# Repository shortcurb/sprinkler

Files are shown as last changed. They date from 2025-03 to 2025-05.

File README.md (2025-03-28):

# sprinkler
For controlling my house sprinklers with a Raspberry Pi and a custom PCB

mqttclient.service handles the MQTT listening for commands and sending responses
sprinklerer.service handles the GPIO pin changing to control different relays
scheduler.service handles checking for weather and sunrise/sunset (solar) data

sprinklerer interacts with other modules purely through redis/celery
I needed an abstraction layer that has exclusive control over the GPIOs to prevent all manner of negative effects with the sprinklers including:
* More than one zone turning on at a time
* Turning more than one zone off at a time (water hammer possible)
* Thinking I turned all the relays/zones off, but then some dormant zombie process coming back and turning one/more back on
* Some other process crashing and leaving the zones turned on forever

scheduler handles 

mqttclient is the only other module that interacts via redis/celery, just adding and cancelling sprinkling and stopping tasks

scheduler handles 

To Do:
* Pull any sensitive info out and put it in a .env and .gitignore it
* Rethink the queuing system. I have no visibility into the Celery thing
    * Maybe there's a way I can handle a queue within python? Have the scheduler spin up a process and do it? Something with async?

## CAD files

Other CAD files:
sprinkler_Fusion360/Sprinkler Case v5.f3d

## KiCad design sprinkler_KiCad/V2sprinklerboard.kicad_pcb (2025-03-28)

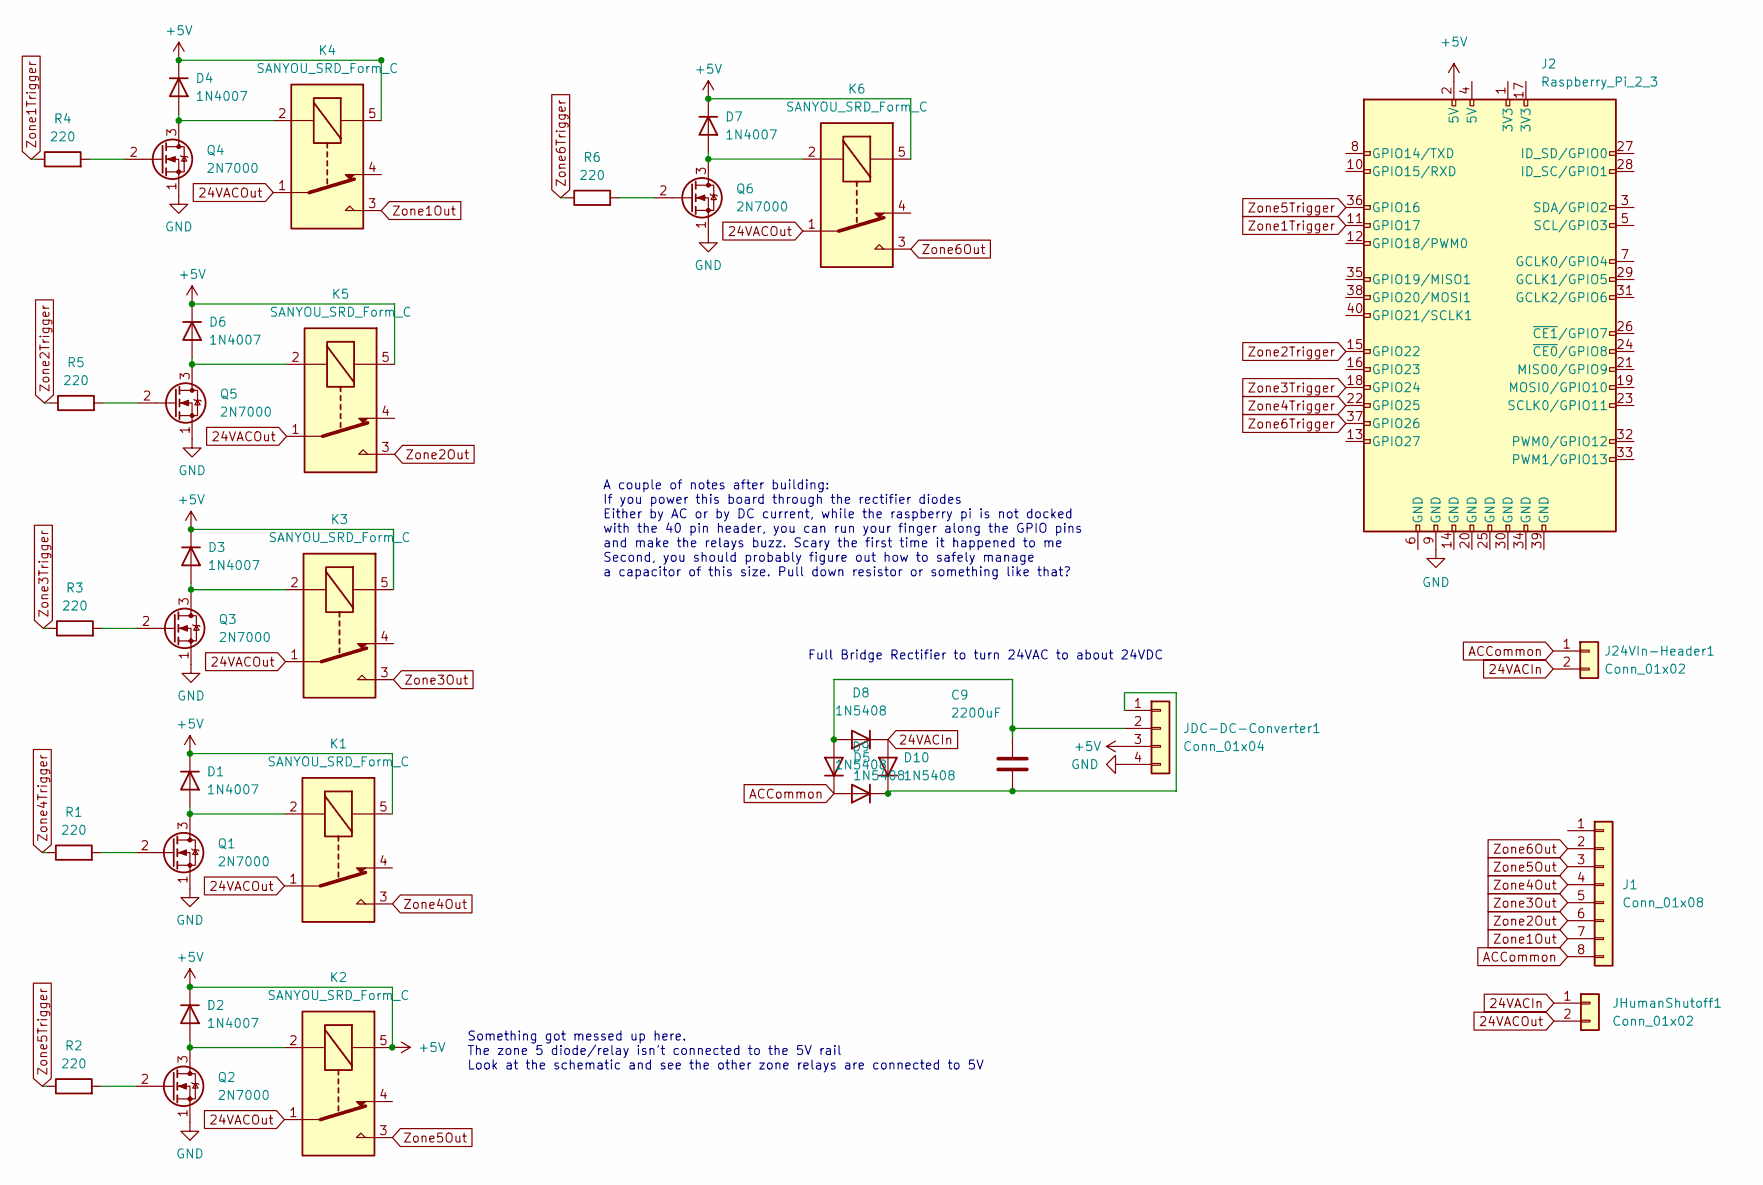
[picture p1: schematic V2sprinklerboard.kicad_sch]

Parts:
C9: 2200uF; C_Radial_D16.0mm_H25.0mm_P7.50mm
D1, D2, D3, D4, D6, D7: 1N4007; D_DO-41_SOD81_P10.16mm_Horizontal
D5, D8, D9, D10: 1N5408; D_DO-201AD_P15.24mm_Horizontal
J1: Conn_01x08; TerminalBlock_Phoenix_MKDS-1,5-8_1x08_P5.00mm_Horizontal
J2: Raspberry_Pi_2_3; RPi Full size -AE
J24VIn-Header1: Conn_01x02; TerminalBlock_Phoenix_MKDS-1,5-2_1x02_P5.00mm_Horizontal
JDC-DC-Converter1: Conn_01x04; XL6009E1 DC-DC
JHumanShutoff1: Conn_01x02; JST_EH_B2B-EH-A_1x02_P2.50mm_Vertical
K1, K2, K3, K4, K5, K6: SANYOU_SRD_Form_C; Relay_SPDT_SANYOU_SRD_Series_Form_C
Q1, Q2, Q3, Q4, Q5, Q6: 2N7000; TO-92_Inline
R1, R2, R3, R4, R5, R6: 220; R_Axial_DIN0411_L9.9mm_D3.6mm_P12.70mm_Horizontal

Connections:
24VACIn: D8.1 (K), D10.2 (A), J24VIn-Header1.2, JHumanShutoff1.1
24VACOut: JHumanShutoff1.2, K1.1, K2.1, K3.1, K4.1, K5.1, K6.1
+5V: D1.1 (K), D3.1 (K), D4.1 (K), D6.1 (K), D7.1 (K), J2.2 (5V), JDC-DC-Converter1.3, K1.5, K3.5, K4.5, K5.5, K6.5
ACCommon: D5.1 (K), D9.2 (A), J1.8 (INT), J24VIn-Header1.1
GND: J2.9 (GND), JDC-DC-Converter1.4, Q1.1 (S), Q2.1 (S), Q3.1 (S), Q4.1 (S), Q5.1 (S), Q6.1 (S)
unnamed: C9.1, D5.2 (A), D8.2 (A), JDC-DC-Converter1.2
unnamed: C9.2, D9.1 (K), D10.1 (K), JDC-DC-Converter1.1
unnamed: D1.2 (A), K1.2, Q1.3 (D)
unnamed: D2.1 (K), K2.5
unnamed: D2.2 (A), K2.2, Q2.3 (D)
unnamed: D3.2 (A), K3.2, Q3.3 (D)
unnamed: D4.2 (A), K4.2, Q4.3 (D)
unnamed: D6.2 (A), K5.2, Q5.3 (D)
unnamed: D7.2 (A), K6.2, Q6.3 (D)
unnamed: Q1.2 (G), R1.2
unnamed: Q2.2 (G), R2.2
unnamed: Q3.2 (G), R3.2
unnamed: Q4.2 (G), R4.2
unnamed: Q5.2 (G), R5.2
unnamed: Q6.2 (G), R6.2
Zone1Out: J1.7 (AD0), K4.3
Zone1Trigger: J2.11 (GPIO17), R4.1
Zone2Out: J1.6 (XDA), K5.3
Zone2Trigger: J2.15 (GPIO22), R5.1
Zone3Out: J1.5 (XCL), K3.3
Zone3Trigger: J2.18 (GPIO24), R3.1
Zone4Out: J1.4 (SDA), K1.3
Zone4Trigger: J2.22 (GPIO25), R1.1
Zone5Out: J1.3 (SCL), K2.3
Zone5Trigger: J2.36 (GPIO16), R2.1
Zone6Out: J1.2 (Pin2), K6.3
Zone6Trigger: J2.37 (GPIO26), R6.1

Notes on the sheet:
A couple of notes after building: If you power this board through the rectifier diodes Either by AC or by DC current, while the raspberry pi is not docked with the 40 pin header, you can run your finger along the GPIO pins and make the relays buzz. Scary the first time it happened to me Second, you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
Something got messed up here. The zone 5 diode/relay isn't connected to the 5V rail Look at the schematic and see the other zone relays are connected to 5V
Full Bridge Rectifier to turn 24VAC to about 24VDC

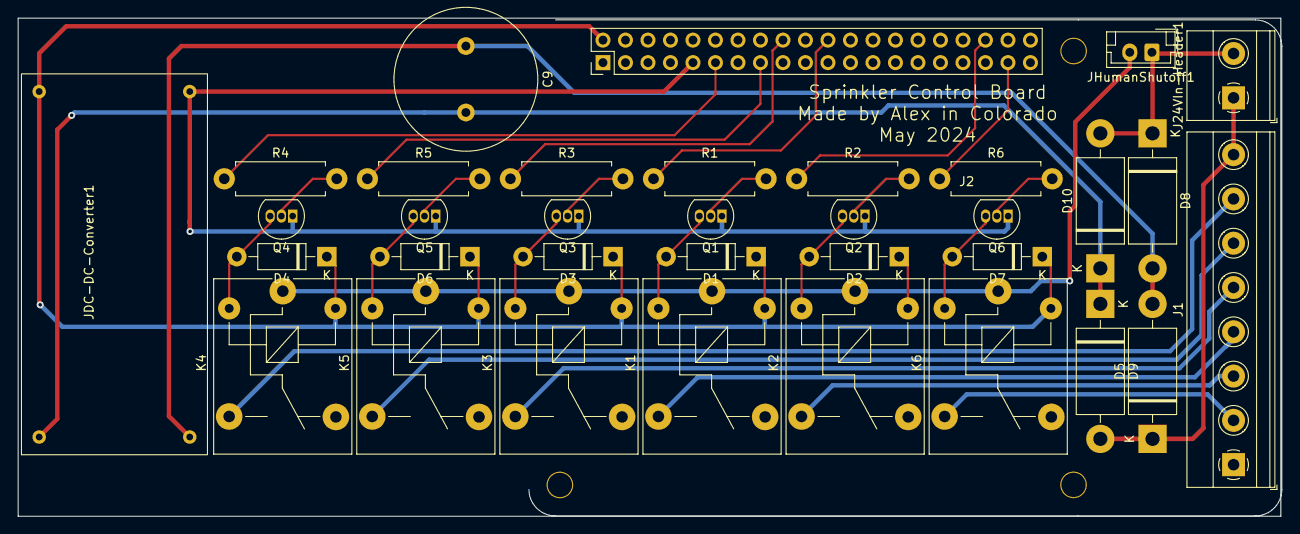
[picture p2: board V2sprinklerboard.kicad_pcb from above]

Board: 2 copper layers, 142.5 x 56.2 mm, 34 parts (0 on the bottom side), 32 nets.

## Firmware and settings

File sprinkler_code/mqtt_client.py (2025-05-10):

import datetime,json,os,traceback,time,asyncio
import paho.mqtt.client as mqtt
from dotenv import load_dotenv
from redis_crud import ScheduleJob, ActiveJob, DataCrud
from gather_data import DataGather


class SprinkleClient:
    def __init__(self):
        load_dotenv()
        self.connected = False
        self.broker_ip = os.environ['mqttbroker']
        self.broker_port = int(os.environ['mqttport'])
        self.username = os.environ['mqttusername']
        self.password = os.environ['mqttpassword']

        self.statetopic = os.environ['mqttsprinklerstatetopic']
        self.cmdtopic = os.environ['mqttsprinklercmdtopic']
        self.responsetopic = os.environ['mqttsprinklerresposnetopic']

        self.commands = ['rain_delay','delay_stop','manual_sprinkle','remove_delay','gather_and_compute', 'skip_next','unskip_next']

    def connect_mqtt(self):
        # Handle reconnection logic elsewhere, just purely connecting here
        if self.connected:
            print('Already connected')
        else:
            self.mqtt_client = mqtt.Client()
            self.mqtt_client.on_message = self.on_message
            self.mqtt_client.on_disconnect=self.on_disconnect
            self.mqtt_client.on_connect = self.on_connect
            self.mqtt_client.username_pw_set(self.username, self.password)
            self.mqtt_client.connect(self.broker_ip, self.broker_port, 60)
            self.connected = True

    def publish_message(self,topic,message):
        if not hasattr(self,'mqtt_client'):
            self.connect_mqtt()

        if isinstance(message,dict):
            message = json.dumps(message,default=str,indent=2)
        try:
            result = self.mqtt_client.publish(topic, message)
        except Exception as e:
            traceback.print_exc()
            self.connected = False
            self.on_disconnect()
            # Let other parts handle the reconnection logic
    
    def gather_and_compute(self,payload):
        print('gathering and computing')
        now = int(time.time())
        sj = ScheduleJob()
        jobs = sj.get_all_jobs()
        job_imminent = False
        for job_id, job_info in jobs.items():
            if job_info['is_cancelled'] !=True and now>job_info['start_at'] and now < job_info['end_at']:
                job_imminent = True
        if job_imminent == False:
            dg = DataGather()
            asyncio.run(self._async_gather_and_compute(dg))

    async def _async_gather_and_compute(self, dg):
        weather_task = asyncio.create_task(dg.get_weather())
        solar_task = asyncio.create_task(dg.get_solar())
        await asyncio.gather(weather_task, solar_task)
        await dg.compute_next_run()

    def delay_stop(self,payload):
        #    payload looks like this: msg = {'command':'delay_stop','value':5,'units':'minutes'}
        # or payload looks like this: msg = {'command':'delay_stop','value':2,'units':'hours'}
        # A delay_stop <=10m is a delay, to be resumed
        # a delay_stop >10m is a stop, with cancellations
        sj = ScheduleJob()
        dc = DataCrud()
        now = int(time.time())
        delay_seconds = datetime.timedelta(**{payload['units']:payload['value']}).total_seconds()
        delay_until = int(now + delay_seconds)
        delay_until_dt = datetime.datetime.now() + datetime.timedelta(seconds = delay_seconds)
        delay_info = {'delay_stop_received_at':now,'delay_stop_until_s':delay_until,'delay_stop_until_dt':delay_until_dt}
        dc.update_data('delaystopinfo',delay_info)
        msg = "Delay/stop request received"
        for job_id,job_info in sj.get_all_jobs().items():
            # if the job isn't cancelled and ( the it starts before the delay or ends before the delay and it hasn't already completed)
            if (job_info['start_at'] < delay_until or job_info['end_at'] < delay_until) and job_info['is_cancelled'] != True and now<job_info['end_at']:
                if delay_seconds <=600:
                    sj.reschedule_existing_job(now,job_id, delay_seconds)
                    msg = f"Delaying until {delay_until_dt}, will resume then"
                else:
                    print('cancelling job',job_id)
                    sj.cancel_job(job_id,now)
                    msg = f"Cancelling jobs through {delay_until_dt}"
                print(msg)
        message = {'received_cmd':'stop','response':msg}
        self.publish_message(self.responsetopic,message)

    def skip_next(self,payload):
        sj = ScheduleJob()
        now = int(time.time())
        next_job_id = None
        next_job_info = {'start_at':now+10**10} 
        
        for job_id,job_info in sj.get_all_jobs().items():
            if job_info['is_cancelled'] == False and job_info['is_active'] == False and job_info['start_at'] > now and now < next_job_info['start_at']:
                next_job_id = job_id
                next_job_info = job_info
                
        print(next_job_id)
#        print('next_job_info',json.dumps(next_job_info,indent=2))
        sj.cancel_job(next_job_id,now)
        message = {'received_cmd':'skip_next','response':f"Skipping next job {next_job_id}"}
        self.publish_message(self.responsetopic,message)

    def unskip_next(self,payload):
        sj = ScheduleJob()
        now = int(time.time())
        next_job_id = None
        next_job_info = {'start_at':now+10**10} 
        for job_id,job_info in sj.get_all_jobs().items():
            if job_info['is_cancelled'] == True and job_info['start_at'] > now and now < next_job_info['start_at']:
                next_job_id = job_id
                next_job_info = job_info
        print(next_job_id)
        sj.uncancel_job(next_job_id)


    def remove_delay(self,payload):
        dc = DataCrud()
        dc.update_data('delaystopinfo',{})

    def manual_sprinkle(self,payload):
    #    payload looks like this: msg = {'command':'manual_sprinkle','value':[[1,5],[2,7],[3,4]],'units':None}
        sj = ScheduleJob()
        now = int(time.time())
        job_info = {
            'start_at':now,
            'zone_info':payload['value'],
            'source':'manual'
                    }
        try:
            job_id = sj.create_job(job_info)
            message = f"Manually created job with id {job_id}"
        except ValueError as e:
            message = e
        self.publish_message(self.responsetopic,{'received_cmd':'manual_sprinkle','response':message})

    def subcribe_loop(self):
#        self.on_disconnect('','','')
        self.connect_mqtt()
        self.mqtt_client.subscribe(self.cmdtopic)
        self.mqtt_client.loop_forever()

    def on_connect(self,client, userdata, flags, rc):
        if rc == 0:
            self.publish_message(self.statetopic,'Posting states here')
            self.publish_message(self.responsetopic,'Starting MQTT client listener')
            self.publish_message(self.cmdtopic,'Listening for commands here')
            print("Connected to broker")
        else:
            print("Connection failed with code", rc)

    def on_disconnect(self,client=None,userdata=None,rc=None):
        self.connected = False
        print('Unexpected disconnection from MQTT broker')
        while self.connected == False:
            try:
                self.connect_mqtt() # connect_mqtt handles setting self.connected to True
                # self.connect_mqtt will also raise an exception if if fails, so put the sleep in the except
                self.subscribe_loop()
            except KeyboardInterrupt:
                return
            except: 
                print('Waiting 5 seconds then attempting reconnection')
#                traceback.print_exc()
                time.sleep(5)

    def on_message(self,client, userdata, msg):
        try:
            payload = msg.payload.decode()
            print(f"Received message: {payload} on topic: {msg.topic}")
            if msg.topic == self.cmdtopic:
                payload = json.loads(payload)
                if payload['command'] in self.commands:
                    getattr(self,payload['command'])(payload) # This calls the given function and executes it with the payload as an argument
        except json.decoder.JSONDecodeError:
            # Only pay attention to json-encoded data
            pass
        except KeyboardInterrupt:
            return
        except Exception as e:
            traceback.print_exc()


if '__main__' == __name__:
    mc = SprinkleClient()
    mc.subcribe_loop()



"""
This thing will have to consist of three separate entities that work together, probably through redis. 
So the structure of data in redis is very important
The sprinkler should handle everything related to atruclly controlling the sprinklers
It will receive a data structure that has a datetime, a list of zones, 
If it has the datetime, is it then the scheduler that decides when to sprinkle?
I guess, yeah. while True: check queue time.sleep(3)
Also I like the idea of keeping datetimes in unix epocs. Makes for easier math
Okay so the sprinkler has a while True loop that checks the queue
The data structure in the queue should be a list of jobs
Jobs should have a datetime start, "active" boolean "cancelled" boolean,
maybe "source" for scheduled vs manual
also datetimes for scheduled at, cancelled at, ran at, etc
Each job needs a unique hash as well

There will also be a redis structure about the current job
When the current job is being executed, it should load that job
into this structure, and update it regularly with current zone,  
time sprinkled, time remaining, next zone, previous zone, expected end datetime
Maybe a cancelled boolean here as well? No.
The cancellation boolean live in the job and the tri-second sprinklerer check the job structure
for cancellation info every 3s?

Then also set up the weather and solar info getting to run via crontab and update redis
And a different (or maybe the same module, different functions?) function
will add jobs to the queue based on solar and weather data
Maybe this system will also clear old jobs out of the queue that are older than e.x. a week?


How do I queue upcoming jobs and make sure they don't overlap?
Maybe I need an intermediary CRUD system that will sit between the job queue
And the systems that might want to CRUD on it?
Yeah I ike that plan
"""




"""

    def delay(self,payload):
    #    payload looks like this: msg = {'command':'delay','value':5,'units':'minutes'}
        now = time.time()
        delay_seconds = datetime.timedelta(**{payload['units']:payload['value']}).total_seconds()
        delay_until = int(now + delay_seconds)
        delay_until_dt = datetime.datetime.now() + datetime.timedelta(**{payload['units']:payload['value']})
        sj = ScheduleJob()
        # don't worry about managing the jobs here
        for job_id,job_info in sj.get_all_jobs():
            if (job_info['start_at'] < delay_until or job_info['end_at'] < delay_until) and job_info['is_cancelled'] != True:
                if job_info['is_active'] == True:
                    print('this is where the computation comes in')
                else:
                    self.sj.reschedule_existing_job(now,job_id,delay_seconds)
            else:
                # really pass, the delay doesn't affect it
                pass
        

    again, what's the interaction between delay and stop?
    A delay implies a resumption,stop implies no resumption
    Maybe have one receipt payload that splits?
    If the payload indicates a timeframe greater than 10 minutes, consider it a stop?
    I think that's it. A delay is, for example to get off the deck when the sprinklers start
    A stop is, e.g. a rain stop or you need to do maintainence on the sprinkler system


 
    def stop(self,payload):
    #    payload looks like this: msg = {'command':'stop':'value':1,'units':'hours}
        now = time.time()
        delay_seconds = datetime.timedelta(**{payload['units']:payload['value']}).total_seconds()
        delay_until = int(now + delay_seconds)
        delay_until_dt = datetime.datetime.now() + datetime.timedelta(**{payload['units']:payload['value']})
        sj = ScheduleJob()
        all_jobs = sj.get_all_jobs()
        for job_id,job_info in all_jobs.items():
            if job_info['start_at'] < delay_until:
                job_info.update({
                    'is_cancelled':True,
                    'cancelled_at':now
                })
                sj.update_job(job_id,job_info)

        # Cancel by creating an immediate job for zone 7 to have a duation of the requested delay_seconds
        # add in stuff about skip for a time to the redis structure that holds that

        msg = {'received_cmd':'stop','response':f"stopping, manual delay until {delay_until_dt}"}
        self.publish_message(self.responsetopic,msg)


"""

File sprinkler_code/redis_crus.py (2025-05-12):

import redis, secrets, string, json,time,traceback
from typing import Dict, Any, List, Optional, Union


class ScheduleJob:
    def __init__(self):
        self.redisclient = redis.Redis(host='localhost', port=6379)

    def uncompute_existing_job(self,job_info): # this is silly
        rudimentary_zones = []
        for item in job_info['zone_info']:
            rudimentary_zones.append([
                item['zone'],(item['end_at']-item['start_at']).total_seconds()/60
            ])
        job_info.update({
            'zone_info':rudimentary_zones,
        })
        return(job_info)

    def reschedule_existing_job(self, now, job_id, delay_s):
        job_info = self.get_job(job_id)
        self.cancel_job(job_id)
        for item in job_info['zone_info']:
            # if the zone hasn't yet been sprinkled, start and end are delayed equally
            # elif the zone is in the middle of being sprinkled, move the start to now + delay and keep the end as end + delay
            # (else) if the zone has already been sprinkled, forget about it
            print(json.dumps(item,indent=2))
            if now < item['on_at'] and now < item['off_at']:
                on_time = item['on_at'] + delay_s
            elif now > item['on_at'] and now < item['off_at']:
                on_time = now + delay_s - 5 # to account for the overlap
            item.update({
                    'on_at':int(on_time),
                    'off_at':int(item['off_at']+delay_s)
                })    
        job_info.update({
            'start_at': int(job_info['zone_info'][0]['on_at']),
            'end_at':int(job_info['end_at'] + delay_s)
        })
        try:
            self.check_for_existing(job_info)
            self.update_job(job_id,job_info)
        except ValueError:
            return('Delayed job interfers with another scheduled job, deleting this one and defering to following. ')

    def compute_new_job(self,job_info):
        start_at = job_info['start_at']
        new_job_info = {
            'start_at':start_at,
            'zone_info':[],
            'source':job_info['source']
        }
        counted_seconds = 0
        for item in job_info['zone_info']:
            duration = item[1] * 60
            zone_info_active = {
                'zone':item[0],
                'on_at':int(start_at + counted_seconds),
                'off_at':int(start_at + counted_seconds + duration + 5)
            }
            new_job_info['zone_info'].append(zone_info_active)
            counted_seconds += duration
        new_job_info.update({
            'end_at':int(start_at + counted_seconds - 5)
        })
        return new_job_info

    def check_for_existing(self,job_id, job_info: Dict):
        job_start = job_info['start_at']
        job_end = job_info['end_at']
        existing_jobs = self.get_all_jobs()

        for existing_job_id,existing_job_info in existing_jobs.items():
            if existing_job_info['is_cancelled'] != True and existing_job_id !=job_id: # only worry about clashes with different jobs and non-cancelled jobs
                if job_start >= existing_job_info['start_at'] and job_start <= existing_job_info['end_at']:
                    raise ValueError(f"Job {job_id} scheduled to start during existing job {existing_job_id}")
                elif (job_end >= existing_job_info['start_at'] and job_end <= existing_job_info['end_at']):
                    raise ValueError(f"Job scheduled to end during existing job {existing_job_id}")

    def get_all_jobs(self):
        jobs = {}
        for key in self.redisclient.scan_iter("jobs:*"):
            job_data = self.redisclient.get(key)
            if job_data:
                jobs.update({key.decode('utf-8'):json.loads(job_data)})
        return jobs       

    def create_job(self,job_info: Dict):
        job_info = self.compute_new_job(job_info)
        try:
            job_id = ''.join(secrets.choice(string.ascii_letters + string.digits) for _ in range(8))
            self.check_for_existing(job_id,job_info)
            job_info.update({
                'created_at':int(time.time()),
                'updated_at':None,
                'cancelled_at':None,
                'is_cancelled':False,
                'is_active':False,
                })
#            print(json.dumps(job_info,indent=2))
            self.redisclient.set(f"jobs:{job_id}",json.dumps(job_info), ex = 60 * 60 * 24 *7)
            return job_id
        except ValueError as e:
            traceback.print_exc()
            print(e)
            return e

    def get_job(self, job_id: str):
        if 'jobs:' not in job_id:
            job_id = f"jobs:{job_id}"
        job_data = self.redisclient.get(job_id)
        if job_data:
            return json.loads(job_data)
        return None

    def update_job(self,job_id: str, update_job: Dict):
        try:
            if update_job['is_cancelled'] != True: # only check for existing if the one you're updating isn't a cancellation
                self.check_for_existing(job_id,update_job)
            update_job.update({'updated_at':int(time.time())})
            self.redisclient.set(job_id,json.dumps(update_job), ex = 60 * 60 * 24 *7)
        except ValueError as e:
            print('i am here')
            traceback.print_exc()

    def cancel_job(self,job_id:str,now=int(time.time())):
        job_info = self.get_job(job_id)
        job_info.update({'is_cancelled':True,'cancelled_at':now})
        self.update_job(job_id,job_info)

    def uncancel_job(self,job_id:str,now=int(time.time())):
        job_info = self.get_job(job_id)
        job_info.update({'is_cancelled':False,'cancelled_at':None})
        self.update_job(job_id,job_info)
        
    def _delete_job(self,job_id:str):
        self.redisclient.delete(job_id)

class ActiveJob:
    def __init__(self):
        self.redisclient = redis.Redis(host='localhost', port=6379)
    
    def get_zone_pin(self):
        return json.loads(self.redisclient.get('zone_pin').decode('utf-8'))

    def update_zone_pins(self,zone_pin):
        self.redisclient.set('zone_pin',json.dumps(zone_pin))

class DataCrud:
    def __init__(self):
        self.redisclient = redis.Redis(host='localhost', port=6379)
        self.redis_ttl = 60 * 60 * 24 *7


    def update_data(self,id,data):
        if isinstance(data,Dict):
            data = json.dumps(data,default=str)
        self.redisclient.set(id,data)
    
    def retrieve_data(self, id):
        data = self.redisclient.get(id)
        if data != None:
            data = json.loads(data)
        return data

if __name__ == '__main__':
    redisclient = redis.Redis(host='localhost', port=6379, decode_responses = True)
    keys = redisclient.keys('*')
#    print(json.dumps(keys,indent=2))
    data = {}
    for key in keys:
        try:
            value = redisclient.get(key)
            data[key] = json.loads(value)
        except Exception as e:
            pass
    print(json.dumps(data,indent=2))
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

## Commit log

2025-03-28 update
    might be some duplicates
    [V2sprinklerboard.kicad_pcb, V2sprinklerboard.kicad_sch]
2025-05-12 added 3d printable case
    [Sprinkler Case v5.f3d]
